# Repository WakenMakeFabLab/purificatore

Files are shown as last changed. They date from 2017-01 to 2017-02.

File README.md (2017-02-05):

### Purificatore d'aria opensource

[fonte](http://www.instructables.com/id/OPEN-SOURCE-AIR-PURIFIER/?ALLSTEPS4)

TODO: tradurre lista dei materiali

inizio progetto: 15 febbraio 2107

Lista materiali:

## 1. Involucro
* 6 fogli (700x400mm) 3 mm multi-plex
* 3 mm plexiglass chiaro
* circa 500 grammi di filamento per stampante 3d

## 2. Componenti elettroniche
* Arduino NANO v3
* 5x 3mmm LED bianco brillante
* 2x 120 mm 12v ventole (pressure optimized)
* 5x resistenze per LED
* Regolatore di tensione 12v in, 5v out
* 12v alimentatore elettrico (1.5A+)
* MQ 135 gas e sensore di fumo
* breadboard
* connettori a 2 pin
* connettori a 5 pin
* cavi

## 3. Filtro d'aria
* Carbone attivo
* Filtro per polvere sottili

## strumenti
* stampante 3d
* Laser cutter
* saldatore e stagno
* Nastro isolante da elettricitsta
* cacciaviate
* pinzette
* Spazzolina
* lacca e altre finiture
* Multi-meter
* Carta vetrata
* colla da legno
* 4x M3 x 40 bulloni
* 2x M3 x 15 bulloni
* distanziatori esagonali
* 1 PC

Costo stimato: 70 euro

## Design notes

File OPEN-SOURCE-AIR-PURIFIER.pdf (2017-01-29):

http://www.instructables.com/id/OPEN-SOURCE-AIR-PURIFIER/technology (http://www.instructables.com/tag/type-id/category-technology/) workshop (http://www.instructables.com/tag/type-id/category-workshop/) craft (http://www.instructables.com/tag/type-id/category-craft/) home (http://www.instructables.com/tag/type-id/category-home/) food (http://www.instructables.com/tag/type-id/category-food/) play (http://www.instructables.com/tag/type-id/category-play/) outside (http://www.instructables.com/tag/type-id/category-outside/) costumes (http://www.instructables.com/tag/type-id/category-costumes/)

# OPEN SOURCE AIR PURIFIER

by ianvanmourik (http://www.instructables.com/member/ianvanmourik/?utm_source=pdf&utm_campaign=title) on May 17, 2016

Table of Contents

## Intro: OPEN SOURCE AIR PURIFIER

Hi y’all,

I'm Ian van Mourik a Product Designer from the Netherlands. This instructable is a brain child that I just had to share with the world. Bad air quality causes various health problems and purification solutions are often complex and expensive. The solution is an open source no nonsense air purifier: the OPEN AIR!

This instructable is based on my first experimental prototype of the OPEN AIR.

It’s meant to be a platform to build upon and improve. My personal goal is to test and improve the design and effectiveness. Collectively we can provide new and better solutions. The modular filter design makes it possible to change and test different kind of filters.

This Design is based on a carbon type filter in collaboration with two pressure optimized 120mm 12v PC fans. It´s controlled by an Arduino with a gas sensor and a LED panel for subtle visual feedback.

If you decide to build your own OPEN SOURCE AIR PURIFIER, be ready to roll up your sleeves, because this won't be an easy one. It will include laser cutting, 3D printing, prototyping, soldering, programming and a lot of other bits and bobs. It will be an advanced instructable. But don't let it scare you, because the reward is big, very big! Like thousands cubic meters of fresh pure clean air big.

Good luck!
Bill of materials:
1. Housing
6 sheets (700x400mm) 3 mm multi-plex 3 mm clear plexiglass
About 500 gram of 3D printer filament
2. Electronics
Arduino NANO v3
5x 3mmm LED bright white
2x 120 mm 12v fans (pressure optimized) 5x LED resistors
Voltage controller 12v in, 5v out
12v power supply (1.5A+)
MQ 135 gas and smoke sensor Prototyping board
2 pin connectors
5 pin connectors
Wires
3. Air Filter
Activated carbon
Fine dust filter
Tools and extra's:

3D Printer
Laser cutter
Soldering iron and Tin
Electrical tape
Screw driver
Nippers
Brush
Varnish or some other paint Multi-meter
Sandpaper
Wood glue
4x M3 x 40 bolts
2x M3 x 15 bolt
Spacer
a PC
and a healthy brain

Total cost: 70 euro

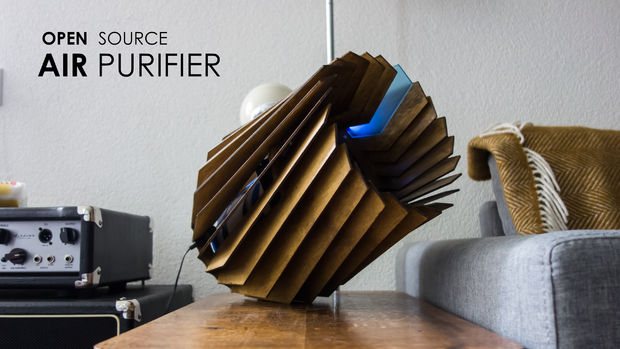
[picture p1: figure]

File Downloads

OPEN AIR_1.1.rar (http://www.instructables.com/files/orig/FWP/MBUH/IPWX52P1/FWPMBUHIPWX52P1.rar) (6 MB)

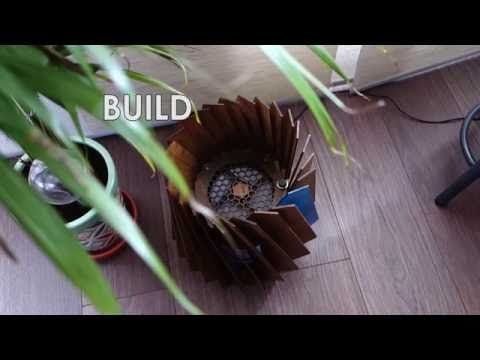
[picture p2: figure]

[NOTE: When saving, if you see .tmp as the file ext, rename it to 'OPEN AIR_1.1.rar'] (http://www.instructables.com/files/orig/FWP/MBUH/IPWX52P1/FWPMBUHIPWX52P1.rar)

## Step 1: Fabrication Frame

The first
step is to fabricate all the parts of the OPEN AIR, beginning with the laser cut wooden frame. I unfortunately do not own a laser cutter :(. But lucky there is a FABLAB nearby: #stadslabrotterdam.

I used 3mm triplex birch wood sheets, birch wood is ideal for laser cutting because it is very soft, and it's cheap witch is always good. Speed and power settings for the laser cutter are depended on the type of wood and machine you are using. Ask the FABLAB crew for help if you are not sure.

You will need one top and one bottom piece, 22 regular ribs, 1 wooden rib with the cutouts for the gas sensor, 1 Plexiglas rib for the LED and a couple of assembly tools.

For the LED rib I used 3mm clear blue Plexiglas which I roughly sanding in a vertical direction. Roughing up clear Plexiglas diffuses the light causing it to light up. Feel free to experiment!

After cutting check everything with a quick test fit, NO GLUE! I would highly recommend cover the wood with some kind of varnish or paint to prevent the wood from warping over time. So sand it down and do whatever you desire. I used heavy duty varnish for a old and kind of dirty finish.

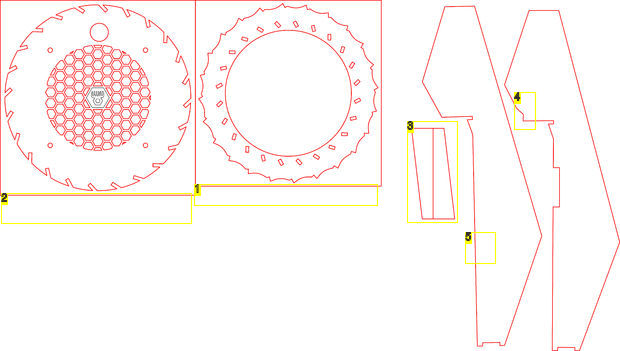
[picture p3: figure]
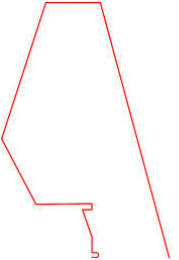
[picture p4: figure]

Image Notes
1. bottom piece
2. top piece
3. assembly tool
4. The special one with cutout for gas sensor and fan wires
5. normal rib. you need 22 of tese

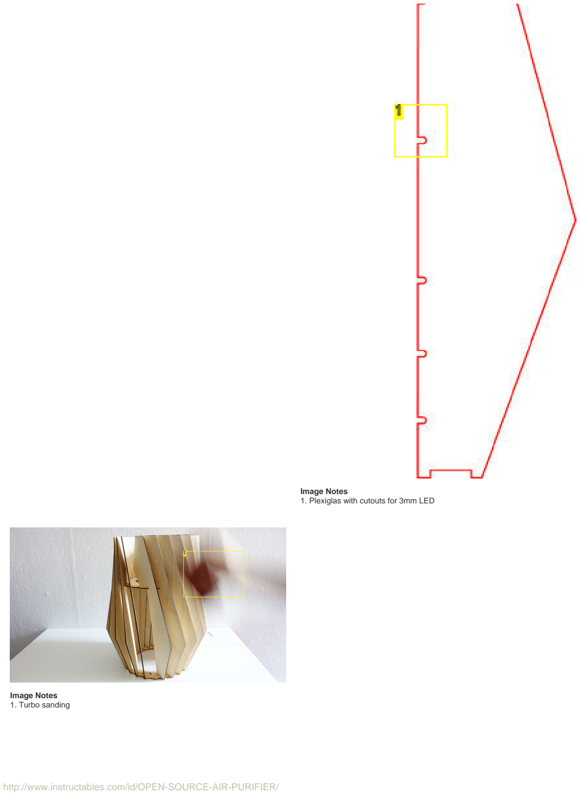
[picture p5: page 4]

Image Notes
1. Plexiglas with cutouts for 3mm LED

Image Notes
1. Turbo sanding

## Step 2: Fabrication 3D printed parts

There are 4 printed parts totaling roughly 24 hours of printing time.

The coupler for the 120mm fans, the coupler for the filer and the filter itself are all printed in the same direction with the same settings. Depending on the printer, the tolerances on the tread can be a bit too tight and may require some sanding to make it fit. All the holes for the M3 bolts should be self-tapping.

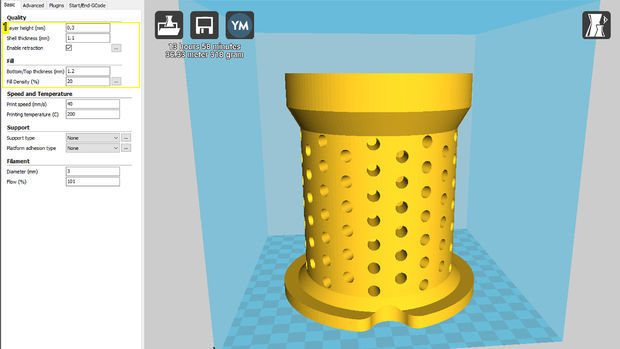
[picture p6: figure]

Image Notes
1. CURA 14.12.1 settings

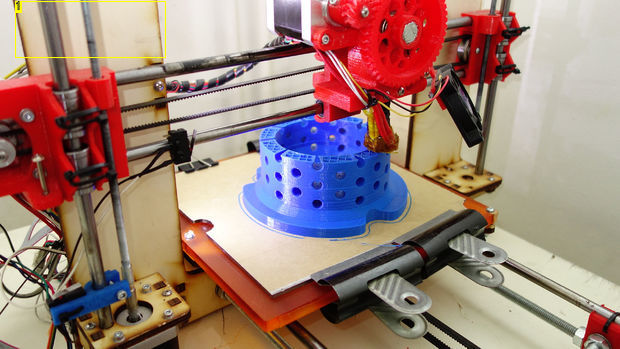
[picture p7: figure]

Image Notes
1. REPRAP Prusra I3.3

## Step 3: Electonics

The open air is made to be
completely autonomous. It has a gas sensor to measure the air quality and a LED panel for visual feedback. My PCB and code is made so there are 3 options:

Clean air: fans and LED are off.

Dirty air: The fans spin near client (speed can be adjusted with a 1K ohm variable resistor) and the LED's breaths slowly in an upwards motion.

Gross air: Fans speed up to maximum and the LED's breaths fast in an upwards motion.

The basic setup of the PCB is made with two relays for the 2 fan speeds. One is direct 12v for full speed and the other is guided though variable resistor.

To provide the Aruino with 5v while using a 12v power supply I used a couple of voltage regulators. This creates a 5v rail for the Arduino and sensor, a 12v rail for the fans and a common ground rail.

The 5 3mm LED's can be glued inside of the cutouts in the Plexiglas. All LED's have the same ground wire, and the positive anode sides will be connected to the Arduino PWM output ports.

LED to Arduino pin connections with resistors. From top to bottom.
pin 3 - 100 ohm
pin 6 - 340 ohm
pin 9 - 220 ohm
pin 10 - 100 ohm
pin 11 - 100 ohm

The resistance varies depending on the thickness of the Plexiglas that the LED has to shine trough.

For maximum ease and customizability everything external is connected with connectors.
Calibration

The MQ sensors are not all the same and needs to be calibrated. Put the sensor near fresh air or ideally outside and wait until the minimum value is reached. This is the value of clean air and you can change the values in the code accordingly. The code is filled with instruction to make it easy to understand where to change the settings.

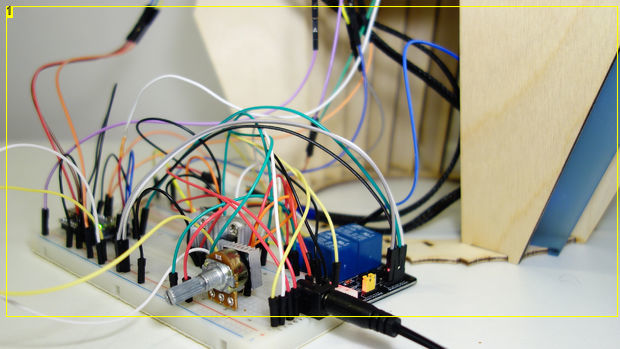
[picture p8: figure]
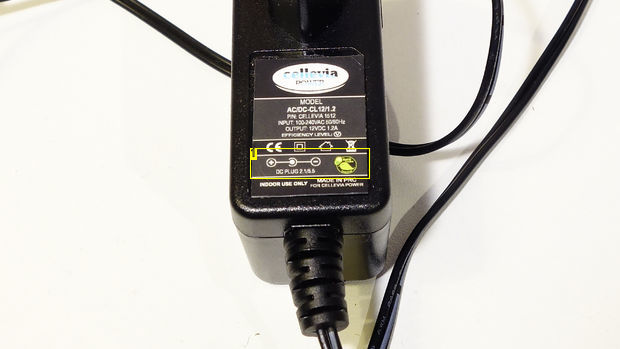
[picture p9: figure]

Image Notes | Image Notes

1. Testing... | 1. polarity indication power supply

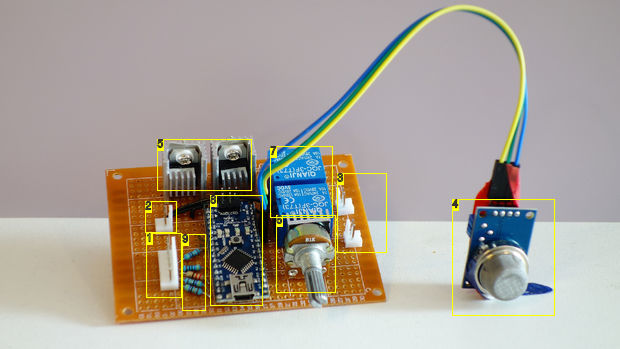
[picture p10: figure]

Image Notes
1. LED connector
2. 12v in
3. 12v FAN out
4. MQ 135 gas sensor
5. 12 to 5 v power regulator + heatsink
6. 1K ohm pod meter
7. DC / DC realais
8. Arduino nano V3
9. LED resisors

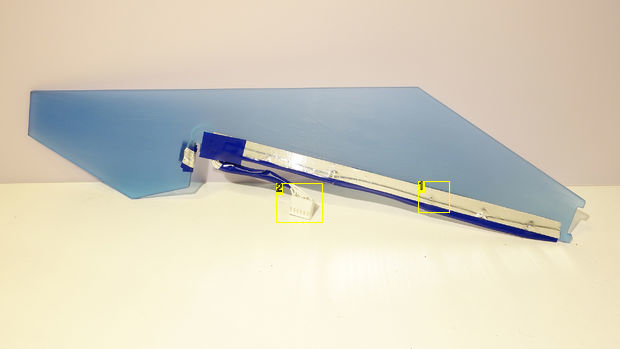
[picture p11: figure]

Image Notes
1. isolating tape layer with a reflective aluminum tape layer
2. 6pin female connector.
one common ground for all 5 LED´s

## Step 4: Assembly part I

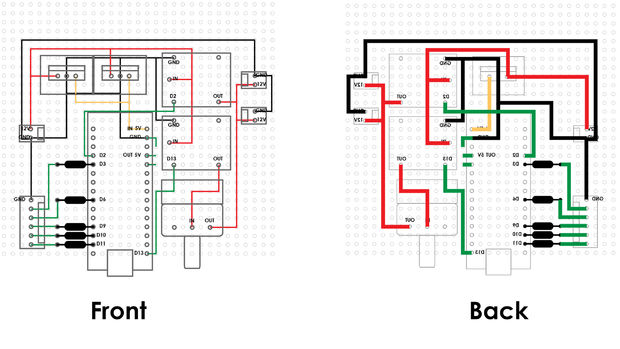
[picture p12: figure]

The assembly is split in to 2 parts because of to many pictures. Before you start the assembly make sure you have all the parts fabricated, painted and ready to go!

Assembly step 1: Fans

First you should build up the fan assembly with the 2 120mm fans, the wooden top piece, dual fan connector, fan to filter connector and the filter housing. Double check the direction of flow of the fans, they need to blow the air upward. 8 M4 40mm bolts is all you need and the bolts can be crewed direly in to the plastic.

Because 3D prints are never completely flat cause of material shrinkage you may need to tighten the bolts quite a bit, remaining gaps between the fans and the printed parts can be covered with tape.

Assembly step 2: lining up

The height of the wooden top piece on top of complete fan assembly is already set. All you need to do is align the bottom piece by putting in 3 ribs and check the angle of the ribs with the assembly tool. If you want to be sure you can put a couple more ribs in and check the whole shape but do NOT glue it all together just jet.

Assembly step 3: The ribs

Important is to leave at least 9 slot open where the sensor hole is located for easy installation of the electronics. And put the one special rib with the sensor cutout and the Plexiglas rib to the side for now.

Start off with 3 ribs in a triangular form like the previous step and triple check the alignment of the bottom piece and the angle of these 3 ribs with the assembly tool before touching any glue. I would recommend to temporarily secure these 3 ribs with tape and then start to work your way around, gluing ribs in place with wood glue.

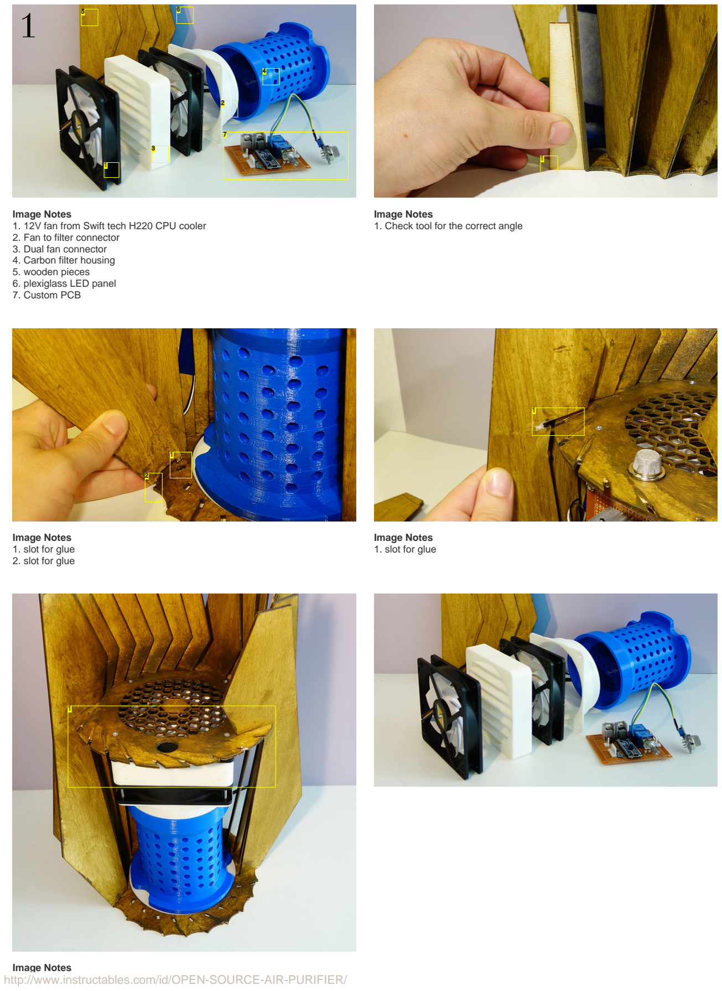
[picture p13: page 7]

Image Notes
1. 12V fan from Swift tech H220 CPU cooler
2. Fan to filter connector
3. Dual fan connector
4. Carbon filter housing
5. wooden pieces
6. plexiglass LED panel
7. Custom PCB

Image Notes
1. Check tool for the correct angle

Image Notes
1. slot for glue
2. slot for glue

Image Notes
1. slot for glue

Image Notes

1. leave at least 9 slots open for easy installation of the electronics

## Step 5: Assembly part II

Assembly step 4: Electronics board.

The electronics board can be mounted in the holes already printed in the fan connector. If you want to you should use the smallest spacers that you can find because the tolerances with the ribs are pretty tight. PRO tip: if the holes in the electronics board won't align with the holes in the printed part, like what append to me.. Get a small screwdriver and a lighter, heat up the screwdriver until it's nice and hot, and then keep rotating the screwdriver while slowly pressing into the printed part. And voila a perfect hole to put a bolt in. keep in mind to not go completely trough the printed part, and you should use 10mm M3 bolts.

Assembly step 5: Finishing up

First let’s finish all the wiring. The fans can be connected and the power plug print can be glued in place after you welded the wires and connector on it. Now is the time to do a last final test to check if the complete system and all the electronics work. If all is well you can start gluing the last ribs in place. I would suggest starting by connecting the LED rib and putting it in place, next I should place the special wooden rib with the cutout for the sensor and the fan wires. Next up is put the remaining 7 ribs in place and BOOM. The main assembly is done!!

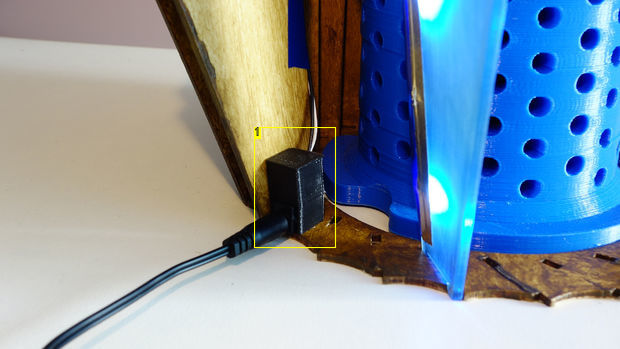
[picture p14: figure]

Image Notes
1. small print for power connector. super glue is king!

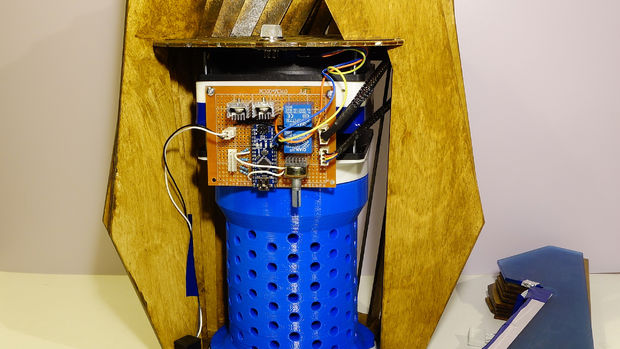
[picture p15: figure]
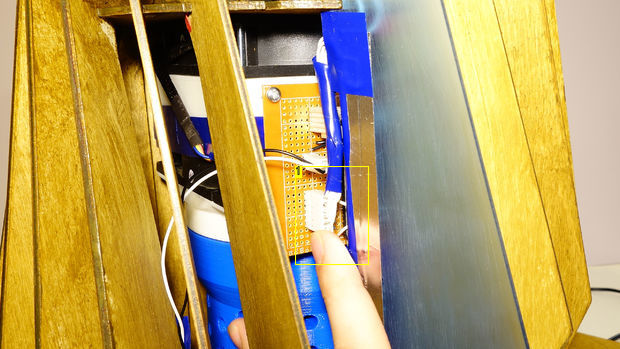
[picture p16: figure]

Image Notes
1. connect the LED´s

## Step 6: The Filter

After the assembly the filter housing can be unscrewed from the bottom of the OPEN AIR.

The trick with using 12v PC fans is to not restrict the air to much by making the filter to dense. Do not overdo it otherwise there would not be enough airflow to have a significant effect on the air quality.

The air will pass through 3 types of media designed to remove dust and toxins from the air

### 1. Fine dust filter

The fine dust filter on the outer side of the housing is the first filter the air encounters and it will remove dust particles from the air. These filters can usually be bought at large stores in the household sections.

### 2. Course activated carbon grid

Activated carbon comes in many shapes and forms and it can be a weird item to find. The simple solution is activated carbon for fish tanks! It's cheap, easy to find and it will work very well as an air purifier. So go to the nearest pet store or go online and search for the biggest grains of activated carbon. The larger the grain the better the airflow!

### 3. Activated carbon sponge

The Activated carbon sponge is also a product made for fish tanks that works great as an air filter medium. The best thing about these sponges is that they are nice and firm and thus can be used as cover, so the activated carbon grid won’t fall out the filter housing. Look for a square sponge at least 8 by 8 centimeters and cut is roughly round so it will fit snugly inside of the filter housing.

A good baseline is the layer design like I illustrated. But feel free to build up your own filter.

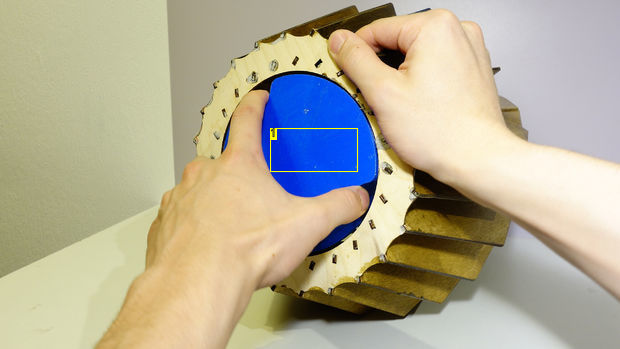
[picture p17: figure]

Image Notes
1. removable filter
righty tighty lefty loosey

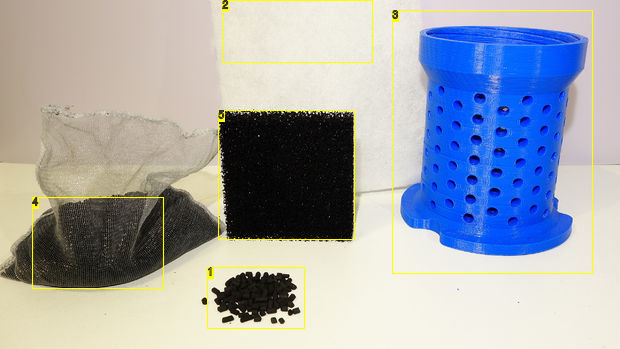
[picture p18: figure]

Image Notes
1. Course activated carbon grid
2. Fine dust filer
3. Housing for carbon type filter
4. Course activated carbon grid
5. Activated carbon sponge

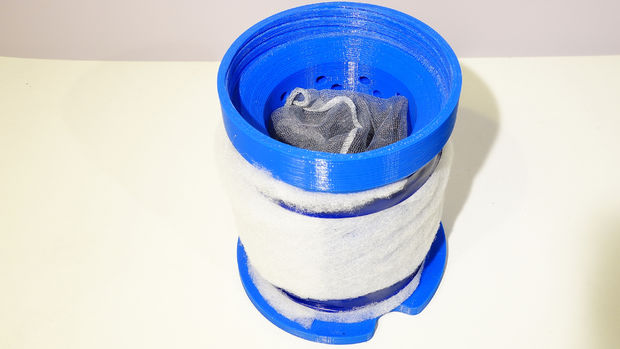
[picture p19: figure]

## Step 7: USE > IMPROVE > SHARE

USE

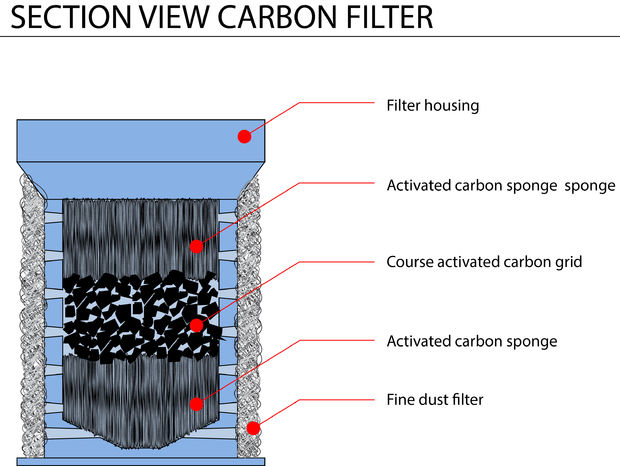
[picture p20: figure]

Great job if you came this far and congratulations on your own OPEN AIR! I hope you did enjoy the build and that you learned some new things along the way.

The open air fits best in a small to medium room like office spaces, bed rooms and living rooms. I would say all the rooms up to a maximum of 35 square meters, otherwise it will be to must of a volume to clean on a constant basis. For use in big rooms the open air can be put on its side to blow a lovely breeze of fresh clean air toward you.

The OPEN AIR with the activated carbon filter will significantly improve the air quality and removes all unwanted odors and toxins from the air. However the activated carbon works like a sponge and will become saturated over time. Meaning that you should replace the activated carbon every once in a while, like every couple of months. Check step 5 for instructions on replacing the filter.

IMPROVE

There are always improvements to be made and this project is no exception. Because the lack of skills and time I could not implement the following improvement:

PWM fan controlled by the gas sensor values.Small control panel for manual override buttons.Overall size of the electronics. Better sensor placement. NOCTUA NF-F12 fans.Different filter designs like: vertex dust chambers, UV sterilization, dehumidifiers, HEPA filers and more

If all goes well in the next time frame, I am going to test the effectiveness of this carbon filter versus a previous UV filter design. Result will be shared of course!

SHARE

I really appreciate all the time and effort that you put in reading, making or improving this instructable! And I really hope you guys are now more aware of the problem of indoor air quality and that you are now a small part of the solution. So share this insturctable and your results and improvements. Together we can make a change!

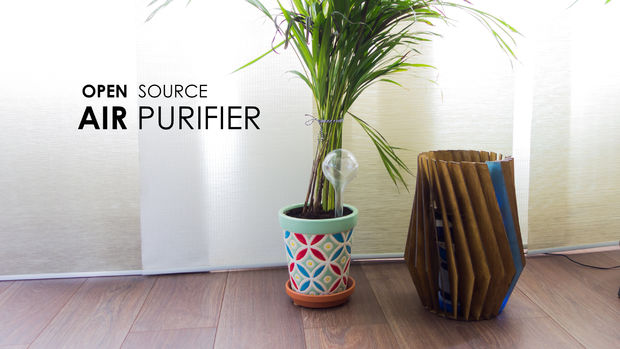
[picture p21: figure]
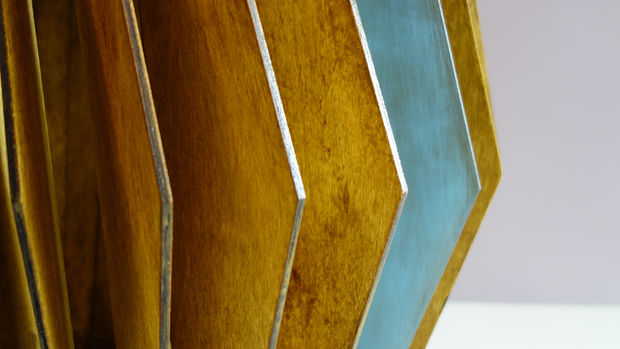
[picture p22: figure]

## Related Instructables

CLEANit : Plant
Powered Air
Purifying
System (http://www.instructables.com/id/CLEANit-Plant-Powered-Air-Purifying-System/) by
Ganesh Varma
Vegesna

Creating
Activated
Carbon From
Food Waste
(CCC Carbon
Method) (http://www.instructables.com/id/Creating-Activated-Carbon-From-Food-Waste-CCC-Car/) by
nocureforcrazy (http://www.instructables.com/member/nocureforcrazy/?utm_source=pdf&utm_campaign=related)

Open Source
Air Purifier :Air
B Development
Timeline : Made
in Shanghai (http://www.instructables.com/id/Air-B-Product-Timeline-Open-Source-Air-Purifier-Ma/) by
aaaiiirrr (http://www.instructables.com/member/aaaiiirrr/?utm_source=pdf&utm_campaign=related)

Activated
Carbon Air
Filter (http://www.instructables.com/id/Activated-Carbon-Air-Filter/?utm_source=pdf&utm_campaign=related) by Hatty (http://www.instructables.com/member/Hatty/?utm_source=pdf&utm_campaign=related)

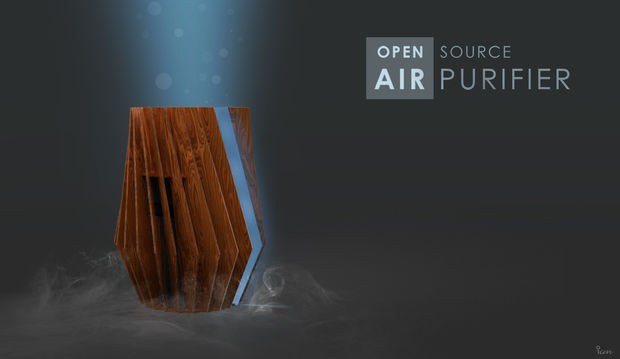
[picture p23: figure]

How to refill a
"disposable"
Brita brand
water pitcher
filter with
activated
carbon. (http://www.instructables.com/id/How-to-refill-a-disposable-Brita-brand-water-pit/) by
IAMSatisfied (http://www.instructables.com/member/IAMSatisfied/?utm_source=pdf&utm_campaign=related)

Open Source 3D
Printed Water
Filter (http://www.instructables.com/id/Open-Source-3D-Printed-Water-Filter/) by
makerboat (http://www.instructables.com/member/makerboat/?utm_source=pdf&utm_campaign=related)

Advertisements

## Comments

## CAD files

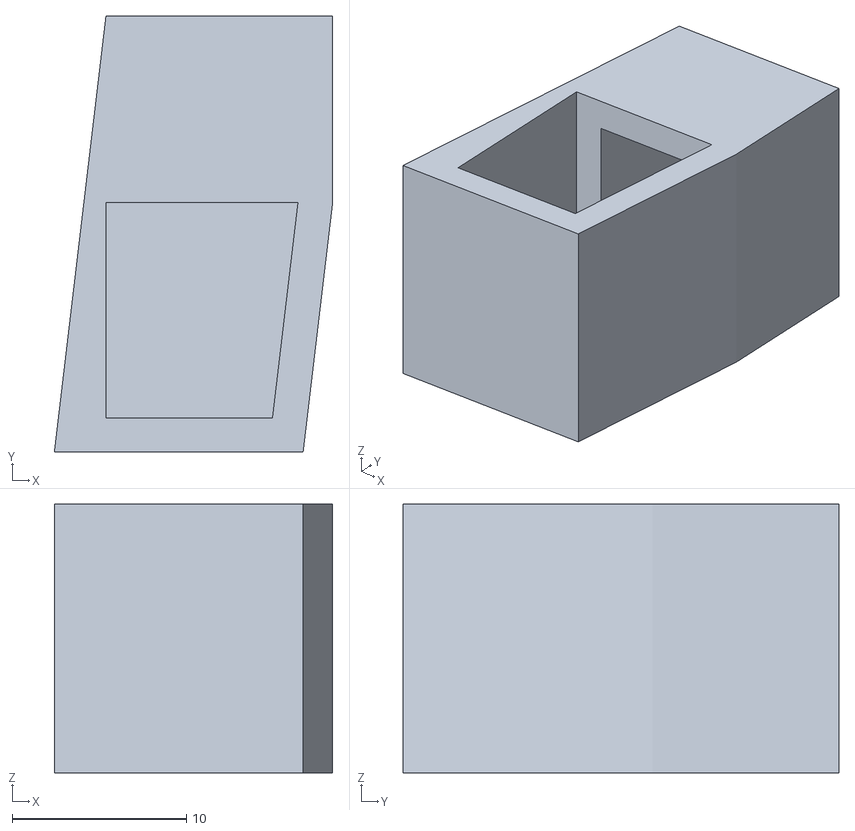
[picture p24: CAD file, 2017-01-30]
3D/OPENAIR_POWERPLUG.STL
16.0 x 25.0 x 15.4

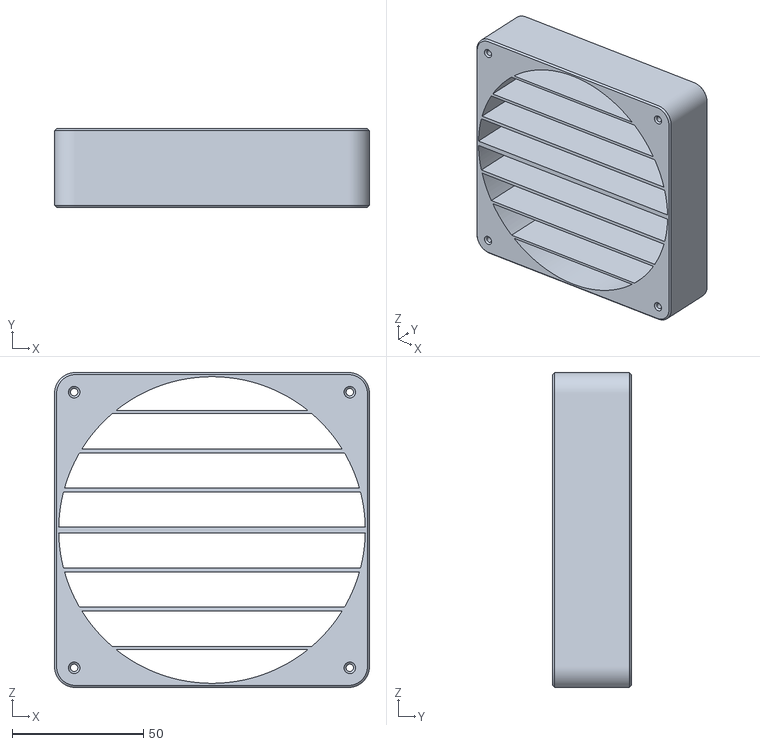
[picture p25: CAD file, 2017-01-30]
3D/OPENAIR_DUAL_FAN_CONNECTOR.STL
120.0 x 30.0 x 120.0

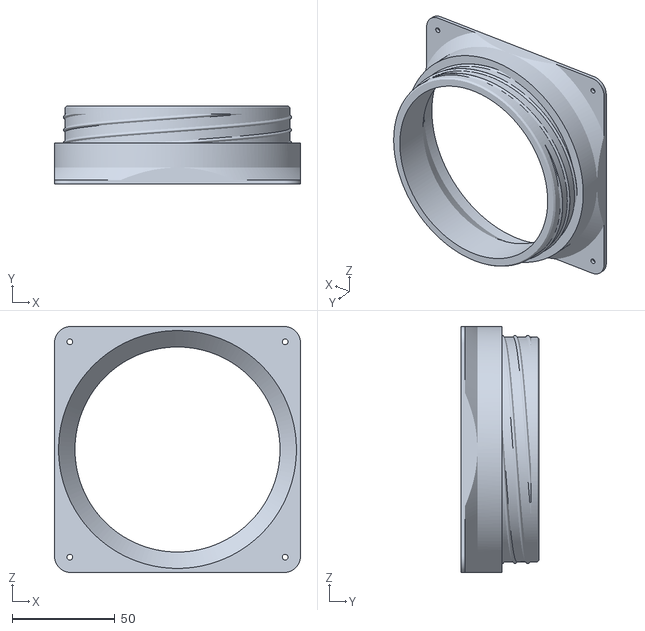
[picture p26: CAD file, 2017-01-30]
3D/OPENAIR_FAN_TO_FILTER_CONNECTOR.STL
120.0 x 38.0 x 120.0

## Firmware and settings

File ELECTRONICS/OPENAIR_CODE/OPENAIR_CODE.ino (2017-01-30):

// LED pins
int value1, value2, value3, value4, value5 ;    // VALEU FOR LATER CALCULATION

//ARDUINO CONNECTION
int ledpin1 = 11;                           
int ledpin2 = 10;                           
int ledpin3 = 9;
int ledpin4 = 6;
int ledpin5 = 3;
long time=0;

// LED Fade timers
int periodeSlow = 5000;     // TIME OF THE SLOW WAVE IN MS
int periodeFast = 1500;     // TIME OF THE FAST WAVE IN MS

//DISPLACEMENT OF THE SLOW WAVE IN MS
int displace2Slow = 500;  
int displace3Slow = 1000;
int displace4Slow = 1500;
int displace5Slow = 2000;

//DISPLACEMENT OF THE FAST WAVE IN MS
int displace2Fast = 150;
int displace3Fast = 300;
int displace4Fast = 450;
int displace5Fast = 600;

// MQ135 gas sensor
float RoA = 10000.0;    // this has to be tuned 10K Ohm WILL INCRESE SENSOR SENSETIVITY
int MQ135 = 7;          // select the input pin for the sensor

int valA = 0;            // variable to store the value coming from the sensor
float VrlA = 0.0;       // variable FOR LATER CALCULATION
float RsA = 0.0;        // variable FOR LATER CALCULATION
float ratioA = 0.0;     // variable FOR LATER CALCULATION
float ppm = 0.0;        // variable FOR LATER CALCULATION

double result;          // variable FOR LATER CALCULATION
double rzero;           // variable FOR LATER CALCULATION

//RELAIS FAN SPEED
 int FanSlow = 4;       // RELAIS 1 pin
 int FanFast = 2;       // RELAIS 2 pin


//Air Qualiti index

int AQI = 0;            // variable FOR LATER CALCULATION
int AQIlast = 0;        // variable FOR LATER CALCULATION
  
  // SENSOR CALIBRATION
float CLEAN = 0.5;      // SENSOR TUNING CLEAN VALUE
float DIRTY = 1.0;      // SENSOR TUNING FAN SLOW VALUE
float GROSS = 2.0;      // SENSOR TUNING FAN FAST VALUE

// TIMERS 
int GROSStimer = 0;
int CLEANtimer = 0;
int x = 1;
int y = 0;
int i = 0;


void setup() {
  
  pinMode(FanSlow, OUTPUT);
  pinMode(FanFast, OUTPUT);


    
Serial.begin(9600);

}

// FINE TUNING SENSOR CALIBREATION 
// original CCalA = 250.6020682  * pow (ratioA, -2.769034857);   

float get_CalA (float ratioA){
  float CalA = 0.0;
  CalA = 250.6020682  * pow (ratioA, -2.769034857);
return CalA;
}

void loop() {

 time = millis();


//MQ135 Sensor valeu read
// get CO ppm

valA = analogRead(MQ135);     // read the value from the analog sensor
VrlA = valA * ( 5.00 / 1024.0  );      // V
RsA = 10000 * ( 5.00 - VrlA) / VrlA ;   // Ohm
ratioA =  RsA/RoA;  
ppm = (get_CalA(ratioA));

//AQI calculation

if ( ppm <= CLEAN){
  AQI = 1;
  CLEANtimer ++;
}

  if ( ppm > CLEAN && ppm < DIRTY ){
  AQI = AQIlast;
}

if ( ppm >= DIRTY && ppm <= (GROSS-0.5)){
  AQI = 2;
}

  if ( ppm > (GROSS-0.5) && ppm < GROSS ){
  AQI = AQIlast;
}

if ( ppm >= GROSS){
  AQI = 3;
  GROSStimer ++;
}




  if  (AQI == 1 && GROSStimer == 0){
    
    digitalWrite(FanSlow, LOW);
    digitalWrite(FanFast, LOW);
    
    value1 = 128+110*cos(2*PI/(periodeSlow)*-time);
    value2 = 128+115*cos(2*PI/periodeSlow*(displace2Slow-time));
    value3 = 128+125*cos(2*PI/periodeSlow*(displace3Slow-time));
    value4 = 128+125*cos(2*PI/periodeSlow*(displace4Slow-time));
    value5 = 128+125*cos(2*PI/periodeSlow*(displace5Slow-time));

    analogWrite(ledpin1, LOW);         
    analogWrite(ledpin2, LOW);          
    analogWrite(ledpin3, LOW);          
    analogWrite(ledpin4, LOW);
    analogWrite(ledpin5, LOW);
      
  }


  else if  (AQI == 2 && GROSStimer == 0){
    
    digitalWrite(FanSlow, HIGH);
    digitalWrite(FanFast, LOW);
  
    value1 = 128+110*cos(2*PI/(periodeSlow)*-time);
    value2 = 128+115*cos(2*PI/periodeSlow*(displace2Slow-time));
    value3 = 128+125*cos(2*PI/periodeSlow*(displace3Slow-time));
    value4 = 128+125*cos(2*PI/periodeSlow*(displace4Slow-time));
    value5 = 128+125*cos(2*PI/periodeSlow*(displace5Slow-time));
    
    analogWrite(ledpin1, value1);           // sets the value (range from 0 to 255)
    analogWrite(ledpin2, value2);           // sets the value (range from 0 to 255)
    analogWrite(ledpin3, value3);           // sets the value (range from 0 to 255)
    analogWrite(ledpin4, value4);           // sets the value (range from 0 to 255)
    analogWrite(ledpin5, value5);           // sets the value (range from 0 to 255)
    
  }

  
  else if  (AQI == 3 && GROSStimer == 0){

    GROSStimer ++;
    digitalWrite(FanSlow, LOW);
    digitalWrite(FanFast, HIGH);
    
    value1 = 128+110*cos(2*PI/(periodeFast)*-time);
    value2 = 128+115*cos(2*PI/periodeFast*(displace2Fast-time));
    value3 = 128+125*cos(2*PI/periodeFast*(displace3Fast-time));
    value4 = 128+125*cos(2*PI/periodeFast*(displace4Fast-time));
    value5 = 128+125*cos(2*PI/periodeFast*(displace5Fast-time));
    
    analogWrite(ledpin1, value1);           // sets the value (range from 0 to 255)
    analogWrite(ledpin2, value2);           // sets the value (range from 0 to 255)
    analogWrite(ledpin3, value3);           // sets the value (range from 0 to 255)
    analogWrite(ledpin4, value4);           // sets the value (range from 0 to 255)
    analogWrite(ledpin5, value5);           // sets the value (range from 0 to 255) 
  
  }

  else if  (GROSStimer > 0){

    GROSStimer ++;
    digitalWrite(FanSlow, LOW);
    digitalWrite(FanFast, HIGH);
    
    value1 = 128+110*cos(2*PI/(periodeFast)*-time);
    value2 = 128+115*cos(2*PI/periodeFast*(displace2Fast-time));
    value3 = 128+125*cos(2*PI/periodeFast*(displace3Fast-time));
    value4 = 128+125*cos(2*PI/periodeFast*(displace4Fast-time));
    value5 = 128+125*cos(2*PI/periodeFast*(displace5Fast-time));
    
    analogWrite(ledpin1, value1);           // sets the value (range from 0 to 255)
    analogWrite(ledpin2, value2);           // sets the value (range from 0 to 255)
    analogWrite(ledpin3, value3);           // sets the value (range from 0 to 255)
    analogWrite(ledpin4, value4);           // sets the value (range from 0 to 255)
    analogWrite(ledpin5, value5);           // sets the value (range from 0 to 255) 
  
  }

  else if ( AQI == 1 && GROSStimer == 0 && CLEANtimer <=5 && ppm <= 1){

  
   for (int y = 0; y > -1; y = y + x)
          analogWrite(ledpin1, y);           // sets the value (range from 0 to 255)
    analogWrite(ledpin2, y);           // sets the value (range from 0 to 255)
    analogWrite(ledpin3, y);           // sets the value (range from 0 to 255)
    analogWrite(ledpin4, y);           // sets the value (range from 0 to 255)
    analogWrite(ledpin5, y);           // sets the value (range from 0 to 255)
    
      if (i == 255) x = -1;             // switch direction at peak
      delay(10);
   

  }

  // TIMER FOR GROSS AIR 
 if ( GROSStimer >= 1000) {   
      GROSStimer = 0;
 }
  if ( CLEANtimer >= 1000) {
      CLEANtimer = 0;
 }


  valA = analogRead(0);       // read analog input pin 0

    Serial.print("| MW135 RAW\t"); 
    Serial.print(valA); 
    Serial.print("\t CO2 concentration\t"); 
    //Serial.print(ppm);
    Serial.print(get_CalA(ratioA));
    Serial.print("\tppm\t");
    Serial.print(AQI); 
    Serial.print("\t");
        Serial.print(GROSStimer); 
    Serial.print("\t");
            Serial.print(CLEANtimer); 
    Serial.print("\t");
    Serial.println();

 AQIlast = AQI;

 
 
 delay (10);
}

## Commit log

2017-01-29 traduzione lista materiali
2017-01-30 finita traduzione lista materiali
2017-01-30 aggiunti materiali di progettazione
    [OPENAIR_DUAL_FAN_CONNECTOR.STL, OPENAIR_FAN_TO_FILTER_CONNECTOR.STL, OPENAIR_POWERPLUG.STL]
2017-02-01 Added list of materials for fab lab
2017-02-05 corretta lista materiali
